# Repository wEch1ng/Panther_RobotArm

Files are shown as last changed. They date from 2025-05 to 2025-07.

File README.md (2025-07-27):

# 一款基于达妙电机和低成本钣金结构件的六轴机械臂

项目初衷是想帮助更多想玩动力学的学生党能玩上低成本的机械臂

有很多同学或RMer实验室有达妙电机，所以方案选择达妙电机，同学们只用出两百五左右的钣金和一些零零碎碎的材料钱就可以了。

基本功能演示视频：https://www.bilibili.com/video/BV1w6dBYxEPu?vd_source=9fd17ff99dc79491d23776f35bfbd4e1

这个仓库仅用于开源最原始的panther机械臂，仅有ros-noetic中一些基本功能：重力补偿模式，拖动示教，基于action通信的moveit轨迹规划
（功能包中的catesian_plan.cpp是调用moveit在笛卡尔空间下画圆，可能有点问题需要自己尝试）

## 相关说明
Panther名字由来：原始设计整机为黑色所以命名为黑豹（Panther），而Panthera是豹类，代表整个Panther机械臂开源项目，希望大家能加入Panthera项目中，创造相对更低成本、性能更好的关节电机方案机械臂，同时实现更多好玩的功能。

## Panthera
后续我们会将Panther从ros中迁移至纯Python环境下来控制

Mujoco仿真及数字孪生

Pinocchio库的使用

diffusion policy模仿学习

强化学习相关内容

跟宇树go2做协同控制

......

后续一些内容的更新在 **Ragtime-LAB** 的Ragtime_Panthera仓库中：
https://github.com/Ragtime-LAB/Ragtime_Panthera

**Ragtime-LAB**目前成员：**亲爱的小一咯**、**小小晨**

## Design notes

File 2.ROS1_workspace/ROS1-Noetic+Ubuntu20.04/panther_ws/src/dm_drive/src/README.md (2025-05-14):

# U2C接入

先插入1-3关节的U2C弹出设备后连接至虚拟机 再插入4-7关节的U2C

ls /dev/ttyACM*
sudo chmod -R 777 /dev/ttyACM*

使用第一条指令

查看是不是弹出

/dev/ttyACM0  /dev/ttyACM1

弹出后再输入第二条指令获得设备使用权限

# 编译工作空间

cd panther_ws/
catkin_make

# 重力补偿

开两个终端分别输入

roscore

rosrun dm_drive ZeroGraMode

# 拖动示教

开两个终端分别输入

roscore

rosrun dm_drive teach

# Moveit控制

开两个终端分别输入

rosrun dm_drive dm_controller

roslaunch panther_moveit_config demo.launch

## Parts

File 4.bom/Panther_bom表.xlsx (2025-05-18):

序号 | 商品名称 | 数量（件） | 单价 | 总计 | 链接
1 | 若干M3螺丝 | 无 | 无 | 无 | https://detail.tmall.com/item.htm?id=601686286684
2 | 若干M3螺母 | 无 | 无 | 无 | 无
 | 橡胶垫片 M3*6*0.8 (200粒) 白 | 1 | 3.4 | 3.4 | https://detail.tmall.com/item.htm?id=20848580632
3 | 达妙4340电机 | 3 | 799 | 2397 | https://item.taobao.com/item.htm?id=775159686012
4 | 达妙4310新手套装 含USB转CAN 转接板 双端线 | 2 | 669 | 1338 | https://item.taobao.com/item.htm?id=730437945135
5 | 达妙4310电机 | 1 | 599 | 599
6 | 达妙3510电机 | 1 | 199 | 199 | https://item.taobao.com/item.htm?abbucket=4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
7 | XT30（2+2）-F母头升级版 | 14 | 1.85 | 25.9 | https://item.taobao.com/item.htm?id=737472229828
8 | 黑色18AWG | 1 | 14 | 14 | https://item.taobao.com/item.htm?id=654286714565
9 | 红色18AWG | 1 | 14 | 14
10 | 黑色28AWG | 1 | 7 | 7
11 | 红色28AWG | 1 | 7 | 7
12 | 滑块 MGW7C（标准块） | 2 | 18 | 36 | https://item.taobao.com/item.htm?id=848276155434&sku_properties=122276018%3A20213
13 | MGW7导轨100MM（备注做成一根200mm的） | 2 | 10 | 20
14 | 1模凸台20齿 内孔10 | 1 | 4.2 | 4.2 | https://detail.tmall.com/item.htm?id=725141098339
15 | 光学平板300x300x13 | 1 | 275 | 275 | https://item.taobao.com/item.htm?from=cart&id=730306309245&skuId=5230836882690&u_channel=null&umpChannel=null
16 | 嘉立创钣金定制 | 5 | 50 | 250 | 立创下单平台
 | 总价 | 5189.5
 | 3D打印材料
 | 兰博abs+
 | https://detail.tmall.com/item.htm?_u=o2rtso892077&id=645580609321&spm=a1z09.2.0.0.40262e8drWVAiV

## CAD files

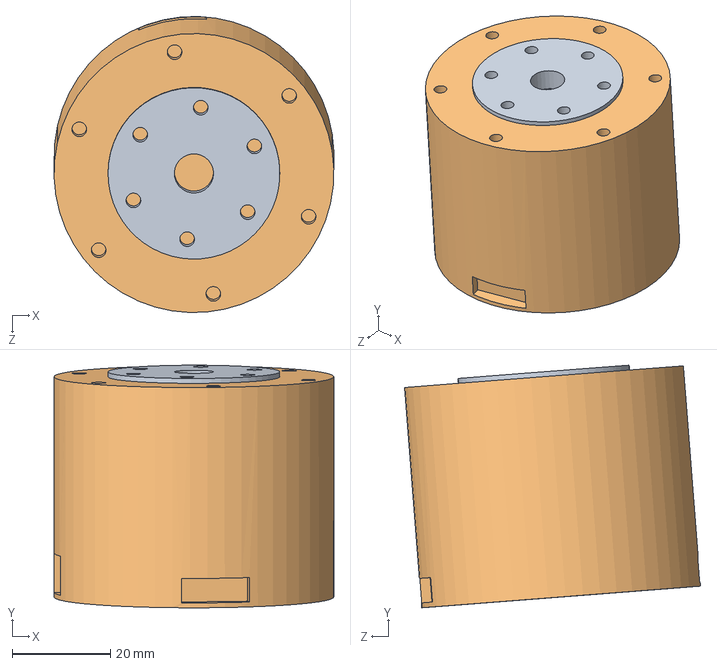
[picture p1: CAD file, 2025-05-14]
1.Model/sw2022/arm/4310电机/4310电机装配体.SLDASM
57.0 x 49.4 x 60.3 mm
4310电机转子
4310电机定子

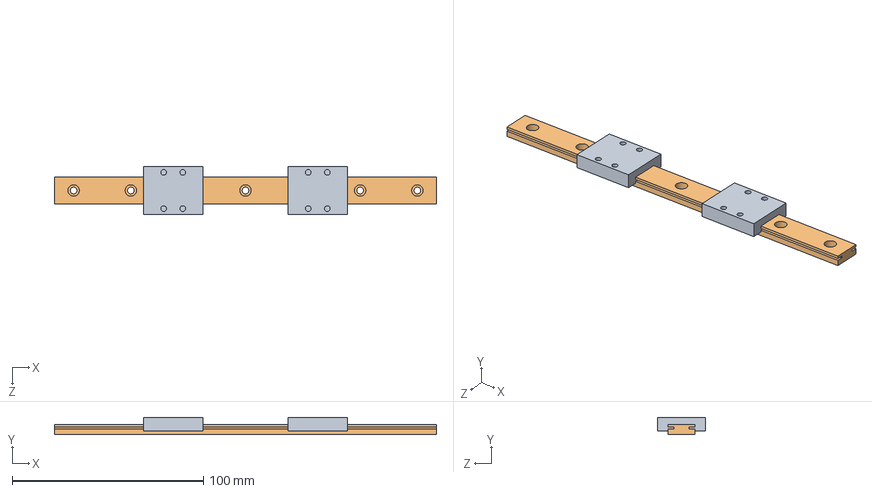
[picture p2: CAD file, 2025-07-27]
1.Model/sw2022/gripper/MGW7导轨滑块模组/MGW7滑轨模组.SLDASM
200.0 x 9.00 x 25.0 mm
MGW7C滑块 x 2
MGW7导轨

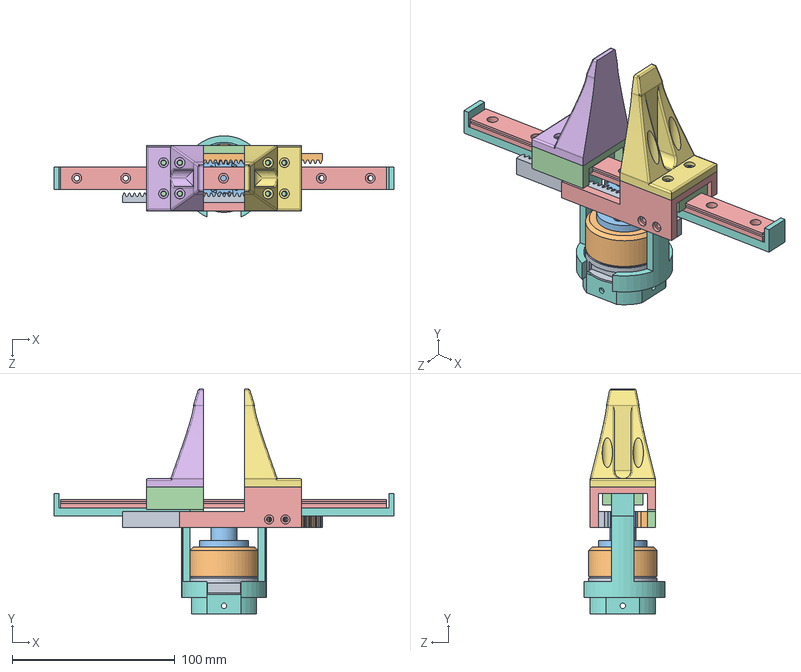
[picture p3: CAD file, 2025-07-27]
1.Model/sw2022/gripper/MyGripper.SLDASM
208.6 x 138.0 x 49.8 mm
3510定子
3510转子
转子齿轮连接件
滑块手指连接件
滑块手指连接件2
手指
镜向手指
夹爪外壳
齿条
齿条2
spur gear_gb
MGW7C滑块 x 2
MGW7导轨

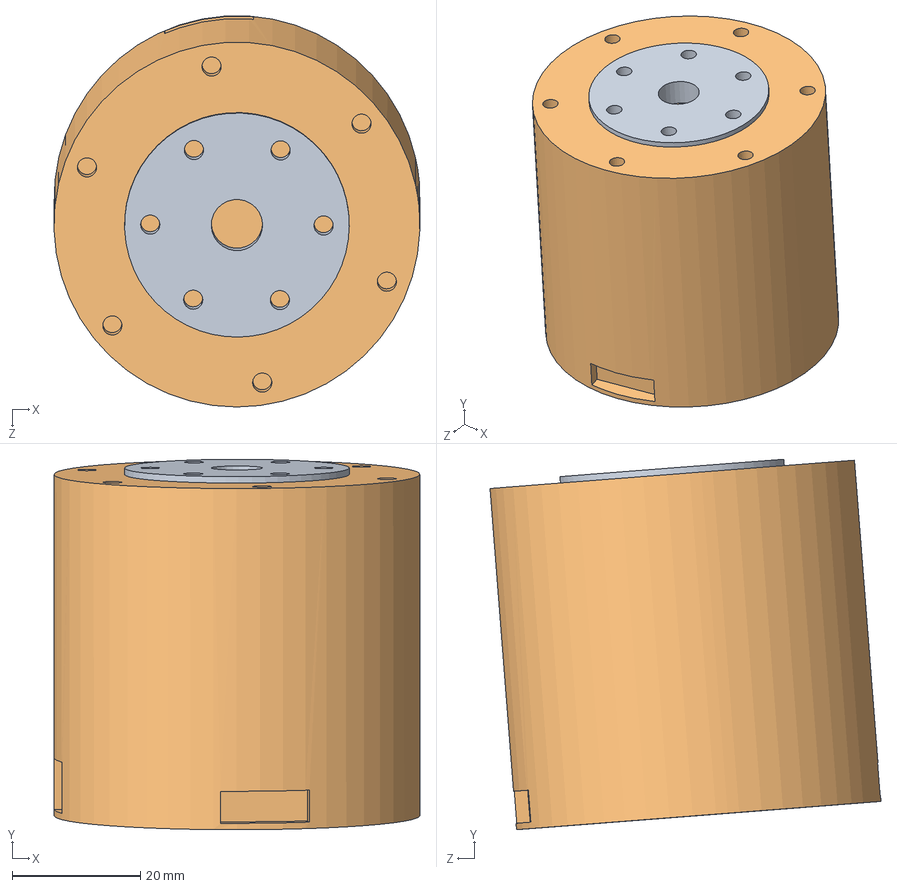
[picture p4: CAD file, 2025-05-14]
1.Model/sw2022/arm/4340电机/4340电机装配体.SLDASM
57.0 x 57.7 x 60.9 mm
4340电机转子
4340电机定子

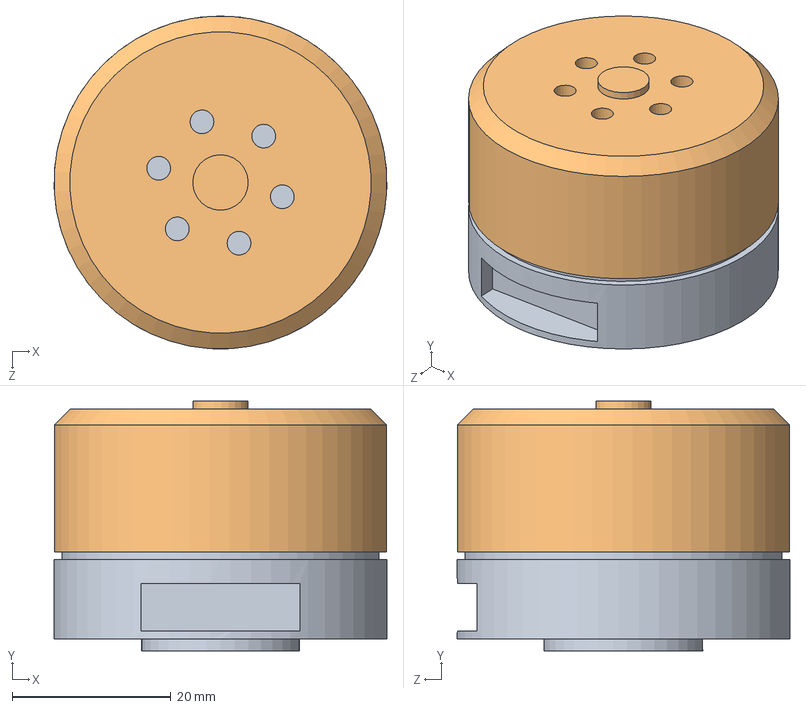
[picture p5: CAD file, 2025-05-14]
1.Model/sw2022/gripper/达妙3510轮毂电机/3510.SLDASM
42.0 x 31.5 x 42.0 mm
3510定子
3510转子

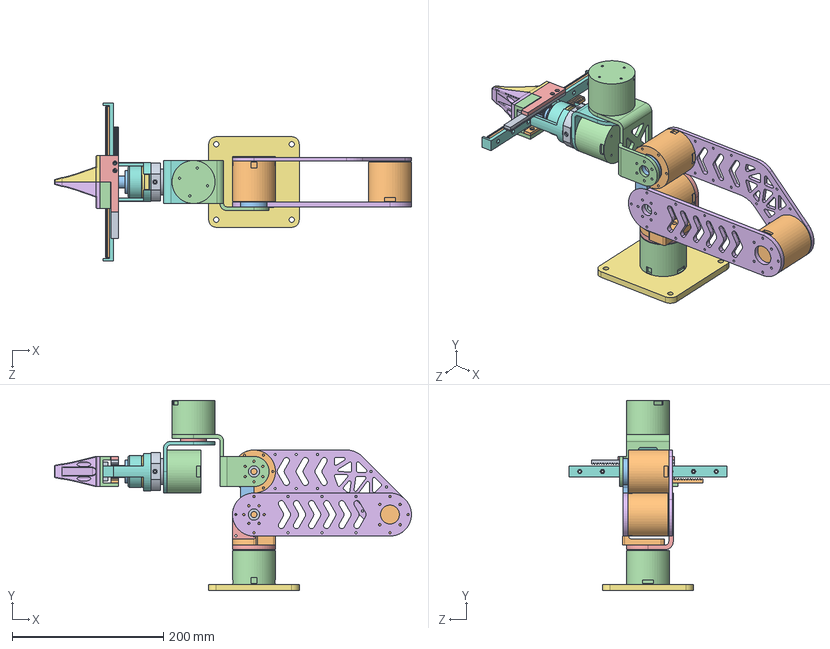
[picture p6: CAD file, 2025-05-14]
1.Model/sw2022/arm/myrobot.SLDASM
472.5 x 251.5 x 208.6 mm
4340电机转子 x 3
4340电机定子 x 3
4310电机转子 x 3
4310电机定子 x 3
一二轴连接件
二三轴连杆
底板
五六轴连接件1
末端法兰
二三轴连杆定位件
四五轴连杆定位件
四五轴连接件_1
五六轴垫块
三四轴连杆
3510定子
3510转子
MGW9C滑块 x 2
MGW9导轨
转子齿轮连接件
滑块手指连接件
滑块手指连接件2
手指
镜向手指
夹爪外壳
齿条
齿条2
spur gear_gb

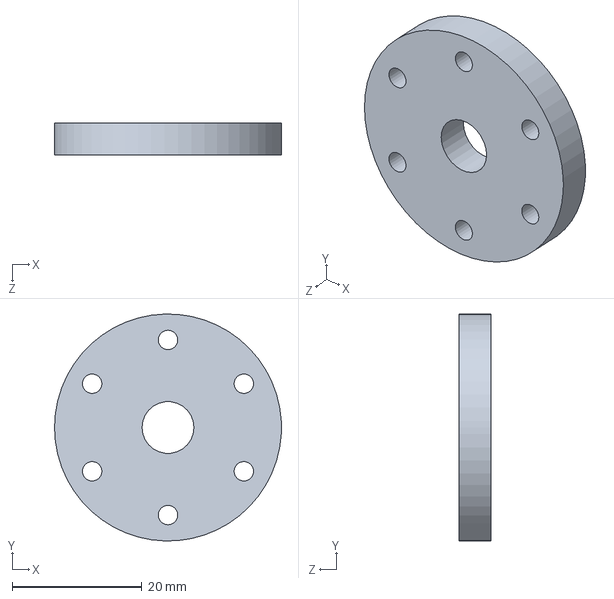
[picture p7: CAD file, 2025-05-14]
1.Model/sw2022/arm/4340电机/4340电机转子.SLDPRT
35.0 x 35.0 x 5.00 mm

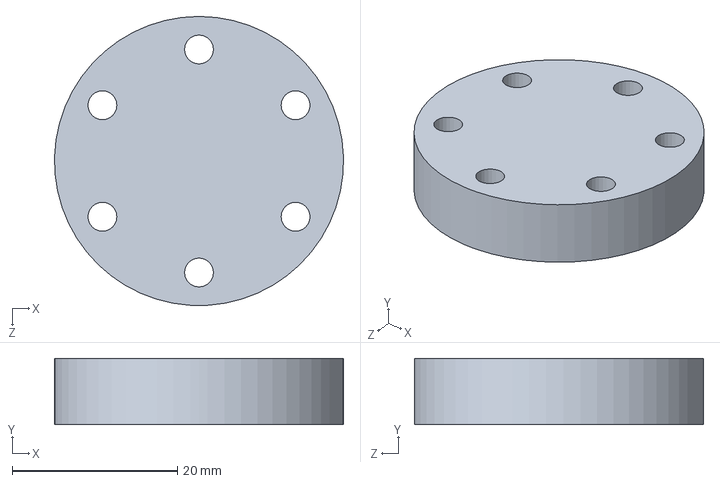
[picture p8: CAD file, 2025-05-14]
1.Model/sw2022/arm/五六轴垫块.SLDPRT
35.0 x 8.00 x 35.0 mm

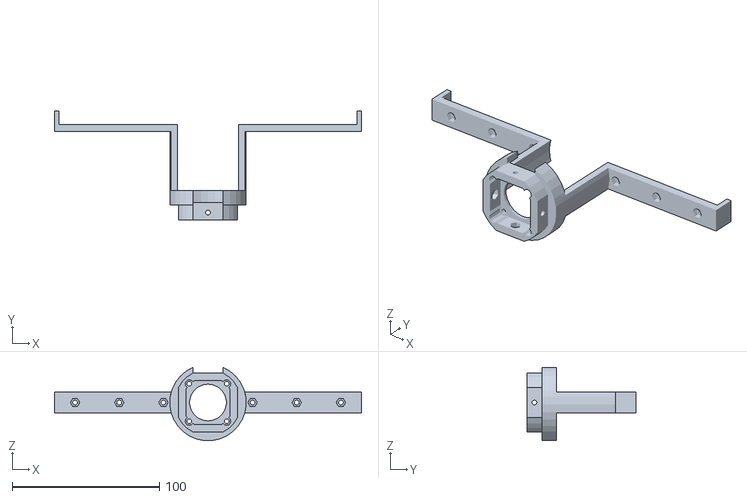
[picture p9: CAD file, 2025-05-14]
1.Model/sw2022/gripper/平行夹爪stl/夹爪外壳.STL
208.6 x 74.0 x 49.7

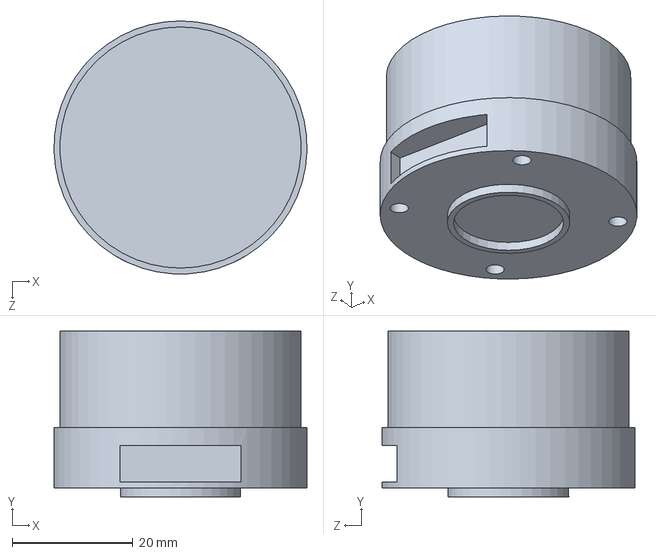
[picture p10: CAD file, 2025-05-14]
1.Model/sw2022/gripper/达妙3510轮毂电机/3510定子.SLDPRT
42.0 x 27.5 x 42.0 mm

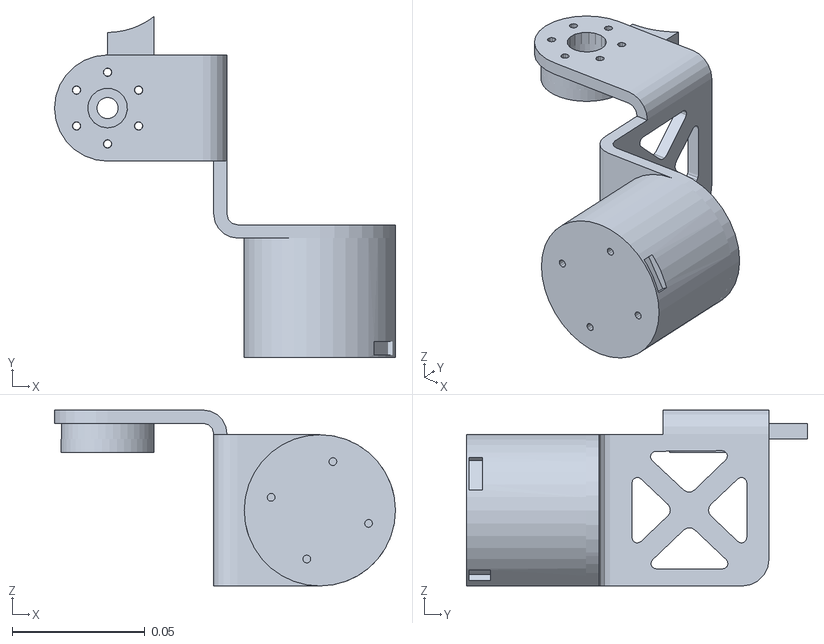
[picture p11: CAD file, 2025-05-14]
2.ROS1_workspace/ROS1-Noetic+Ubuntu20.04/panther_ws/src/panther_description/meshes/link4.STL
0.129 x 0.129 x 0.0663

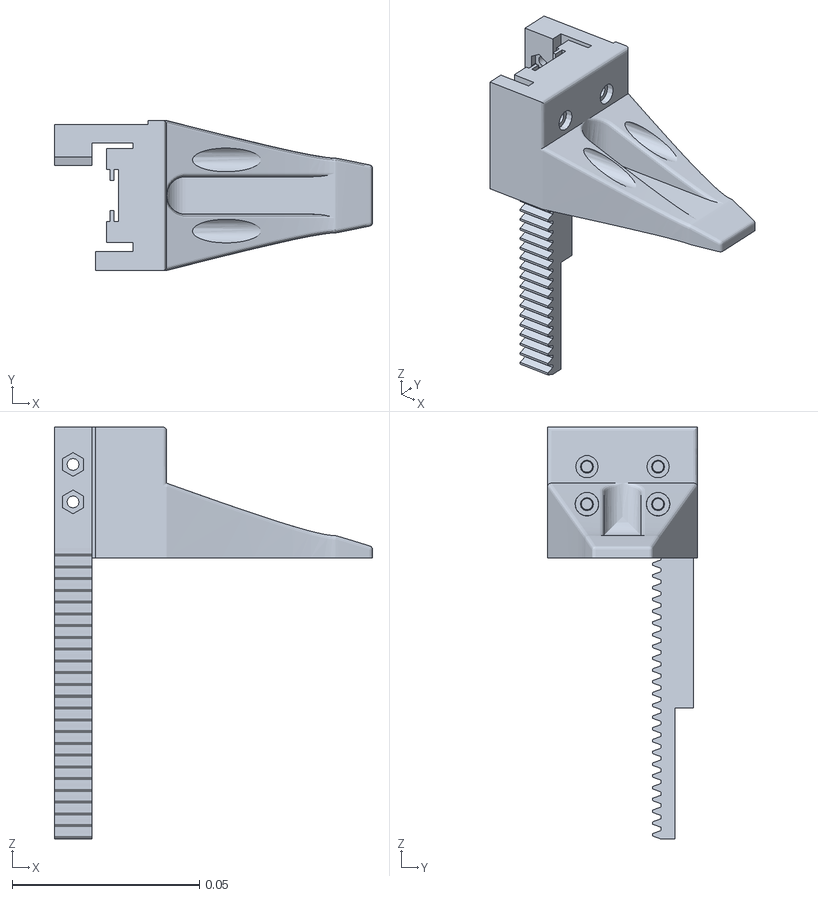
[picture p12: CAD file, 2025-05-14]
3.sw2urdf/panther_description/meshes/gripper_1_link.STL
0.085 x 0.04 x 0.11

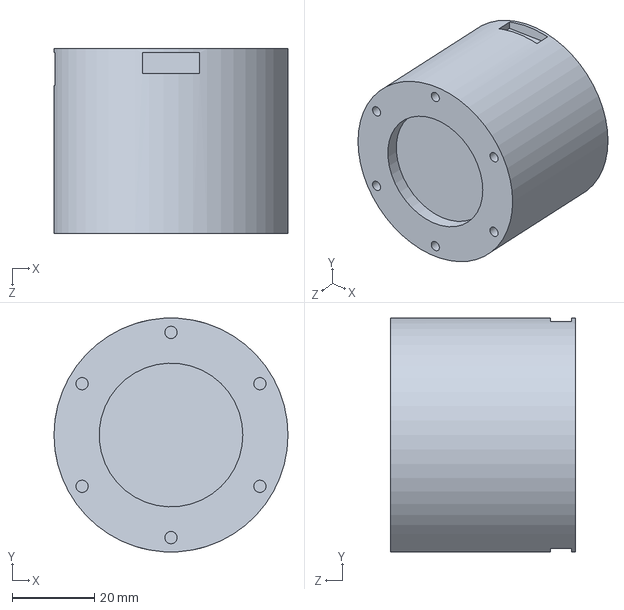
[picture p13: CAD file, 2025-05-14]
1.Model/sw2022/arm/4310电机/4310电机定子.SLDPRT
57.0 x 56.9 x 45.0 mm

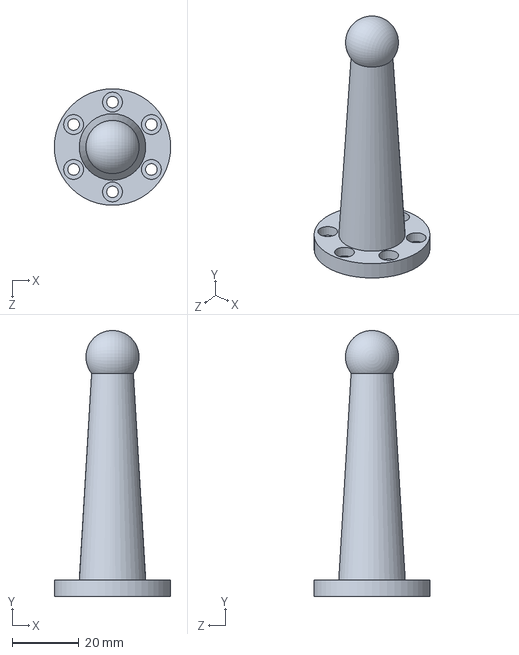
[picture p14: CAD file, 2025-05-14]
1.Model/sw2022/arm/圆头末端.SLDPRT
35.0 x 80.0 x 35.0 mm

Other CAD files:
1.Model/sw2022/arm/装配体1.SLDASM
1.Model/Step/PantherGripper.STEP
1.Model/sw2022/gripper/MGW7导轨滑块模组/MGW7C滑块.SLDPRT
1.Model/sw2022/gripper/平行夹爪stl/齿条.STL
1.Model/sw2022/arm/4310电机/4310电机转子.SLDPRT
1.Model/sw2022/arm/4340电机/4340电机定子.SLDPRT
1.Model/sw2022/arm/一二轴连接件.SLDPRT
1.Model/sw2022/arm/三四轴连杆.SLDPRT
1.Model/sw2022/arm/二三轴连杆.SLDPRT
1.Model/sw2022/arm/二三轴连杆定位件.SLDPRT
1.Model/sw2022/arm/五六轴连接件1.SLDPRT
1.Model/sw2022/arm/从动轴.SLDPRT
1.Model/sw2022/arm/四五轴连接件.SLDPRT
1.Model/sw2022/arm/四五轴连接件_1.SLDPRT
1.Model/sw2022/arm/四五轴连杆定位件.SLDPRT
1.Model/sw2022/arm/底板.SLDPRT
1.Model/sw2022/gripper/1模20齿凸台齿轮.SLDPRT
1.Model/sw2022/gripper/GB - Spur gear 1M 20T 20PA 10FW ---S20A75H50L1.0N.SLDPRT
1.Model/sw2022/gripper/GB - Spur gear 1M 20T 20PA 10FW ---S20B16H18L10.0N.SLDPRT
1.Model/sw2022/gripper/MGW7导轨滑块模组/MGW7导轨.SLDPRT
1.Model/sw2022/gripper/rack spur rectangular_gb.SLDPRT
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

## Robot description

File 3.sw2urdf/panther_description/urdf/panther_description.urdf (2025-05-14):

<?xml version="1.0" encoding="utf-8"?>
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
<robot name="panther_description">
  <link name="base_link">
    <inertial>
      <origin xyz="-5.22421768267327E-17 -4.9646319201852E-06 0.00682594884114425" rpy="0 0 0" />
      <mass value="1.00980967249859" />
      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
    </inertial>
    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
  </link>
  <link name="link1">
    <inertial>
      <origin xyz="-0.000140138460727448 -0.0115178455380478 -0.0189175974816606" rpy="0 0 0" />
      <mass value="0.433540348958132" />
      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
    </inertial>
    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
  </link>
  <joint name="joint1" type="revolute">
    <origin xyz="0 0 0.1005" rpy="0 0 0" />
    <parent link="base_link" />
    <child link="link1" />
    <axis xyz="0 0 1" />
    <limit lower="-3.14" upper="3.14" effort="3" velocity="1" />
  </joint>
  <link name="link2">
    <inertial>
      <origin xyz="0.106425438295557 -3.80251385934116E-12 0.0236077558477278" rpy="0 0 0" />
      <mass value="0.618785138060723" />
      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
    </inertial>
    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
  </link>
  <joint name="joint2" type="revolute">
    <origin xyz="0 0 0" rpy="1.5707963267949 0 3.14159265358979" />
    <parent link="link1" />
    <child link="link2" />
    <axis xyz="0 0 1" />
    <limit lower="-3.14" upper="3.14" effort="3" velocity="1" />
  </joint>
  <link name="link3">
    <inertial>
      <origin xyz="0.112947841031452 0.0109257169593898 0.0234930652223882" rpy="0 0 0" />
      <mass value="0.578438290721478" />
      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
    </inertial>
    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
  </link>
  <joint name="joint3" type="revolute">
    <origin xyz="0.179999999999998 0 0" rpy="3.14159265358979 0 2.83491633418811" />
    <parent link="link2" />
    <child link="link3" />
    <axis xyz="0 0 1" />
    <limit lower="-3.14" upper="3.14" effort="3" velocity="1" />
  </joint>
  <link name="link4">
    <inertial>
      <origin xyz="0.0513406245602283 -0.0329058384127011 0.00868209734629183" rpy="0 0 0" />
      <mass value="0.399529174718196" />
      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
    </inertial>
    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
  </link>
  <joint name="joint4" type="revolute">
    <origin xyz="0.188809427730714 0 0" rpy="3.14159265358979 0 -0.306676319401685" />
    <parent link="link3" />
    <child link="link4" />
    <axis xyz="0 0 1" />
    <limit lower="-3.14" upper="3.14" effort="3" velocity="1" />
  </joint>
  <link name="link5">
    <inertial>
      <origin xyz="2.62314297356869E-16 -0.0160776069634142 -0.0180581657290753" rpy="0 0 0" />
      <mass value="0.321861622200536" />
      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
    </inertial>
    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
  </link>
  <joint name="joint5" type="revolute">
    <origin xyz="0.08 0 0" rpy="-1.5708 1.5708 0" />
    <parent link="link4" />
    <child link="link5" />
    <axis xyz="0 0 1" />
    <limit lower="-3.14" upper="3.14" effort="3" velocity="1" />
  </joint>
  <link name="link6">
    <inertial>
      <origin xyz="-4.35824622879912E-15 -2.3037127760972E-15 -0.0025000000000041" rpy="0 0 0" />
      <mass value="0.00434717883440458" />
      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
    </inertial>
    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
  </link>
  <joint name="joint6" type="revolute">
    <origin xyz="0 -0.036 0" rpy="1.5708 0 0" />
    <parent link="link5" />
    <child link="link6" />
    <axis xyz="0 0 1" />
    <limit lower="-3.14" upper="3.14" effort="3" velocity="1" />
  </joint>
  <link name="gripper_centor_link">
    <inertial>
      <origin xyz="-0.107107907434468 -0.000284330630565321 -3.59780083918573E-09" rpy="0 0 0" />
      <mass value="0.105344961426715" />
      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
    </inertial>
    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
  </link>
  <joint name="gripper_centor_joint" type="fixed">
    <origin xyz="0 0 0.148" rpy="0 -1.5708 0" />
    <parent link="link6" />
    <child link="gripper_centor_link" />
    <axis xyz="0 0 0" />
    <limit lower="-3.14" upper="3.14" effort="3" velocity="1" />
  </joint>
  <link name="gripper_1_link">
    <inertial>
      <origin xyz="-0.0574118738630709 0.00266477929541095 0.00735600840817693" rpy="0 0 0" />
      <mass value="0.0426889603072748" />
      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
    </inertial>
    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
  </link>
  <joint name="gripper_1_joint" type="prismatic">
    <origin xyz="0 0 0.148" rpy="0 -1.5708 0" />
    <parent link="link6" />
    <child link="gripper_1_link" />
    <axis xyz="0 0 1" />
    <limit lower="0" upper="0.06" effort="0.18" velocity="1" />
  </joint>
  <link name="gripper_2_link">
    <inertial>
      <origin xyz="-0.0573873207529981 -0.00294326456557495 -0.00756965143896882" rpy="0 0 0" />
      <mass value="0.0427537416759649" />
      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
    </inertial>
    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
  </link>
  <joint name="gripper_2_joint" type="prismatic">
    <origin xyz="0 0 0.148" rpy="0 -1.5708 0" />
    <parent link="link6" />
    <child link="gripper_2_link" />
    <axis xyz="0 0 1" />
    <limit lower="0" upper="0.06" effort="0.18" velocity="1" />
    <mimic joint="gripper_1_joint" multiplier="-1" offset="0" />
  </joint>
</robot>

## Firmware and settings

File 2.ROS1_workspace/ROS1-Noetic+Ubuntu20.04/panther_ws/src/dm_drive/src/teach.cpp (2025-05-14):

#include "ros/ros.h"
#include "6Dof_dyna.h"
#include "damiao.h"
#include "unistd.h"
#include <cmath>
#include <algorithm> // for std::max and std::min
#include <iostream>  // for std::cout
#include <thread>
#include <boost/thread/shared_mutex.hpp>
#include "sensor_msgs/JointState.h"
#include <vector>
#include <fstream>
#include <atomic>
#include <array>


// 硬件控制参数
constexpr double RECORD_RATE = 500.0;    // 记录频率
constexpr double RECORD_DURATION = 20.0; // 记录时长
constexpr double RETURN_SPEED = 0.5;     // 返回速度比例

// 单个关节状态数据结构
struct JointState {
    double position;    // 关节位置（弧度）
    double velocity;    // 关节速度（弧度/秒）
};

// 单帧数据（所有关节+时间戳）
struct JointFrame {
    double timestamp;   // 时间戳（相对于记录开始时间）
    std::array<JointState, 7> joints; // 6个关节状态
};

// 全局数据存储
std::vector<JointFrame> motion_buffer; // 动作数据缓冲区
std::array<double, 7> initial_positions; // 初始关节位置（弧度）

// 硬件控制对象
damiao::Motor M1(damiao::DM4310,0x01, 0x11);
damiao::Motor M2(damiao::DM4340,0x02, 0x12);
damiao::Motor M3(damiao::DM4340,0x03, 0x13);
damiao::Motor M4(damiao::DM4340,0x04, 0x14);
damiao::Motor M5(damiao::DM4310,0x05, 0x15);
damiao::Motor M6(damiao::DM4310,0x06, 0x16);
damiao::Motor M7(damiao::DMH3510,0x07, 0x17);

damiao::Motor motors[] = {M1, M2, M3, M4, M5, M6, M7};

// boost::shared_mutex serial_mutex_;  
std::shared_ptr<SerialPort> serial1;
std::shared_ptr<SerialPort> serial2;
damiao::Motor_Control dm1(serial1);
damiao::Motor_Control dm2(serial2);

void add_all_motors(){
    dm1.addMotor(&M1);
    dm1.addMotor(&M2);
    dm1.addMotor(&M3);
    dm2.addMotor(&M4);
    dm2.addMotor(&M5);
    dm2.addMotor(&M6);
    dm2.addMotor(&M7);
}

void change_motor_mode_MIT(){
    dm1.switchControlMode(M1,damiao::MIT_MODE);
    dm1.switchControlMode(M2,damiao::MIT_MODE);
    dm1.switchControlMode(M3,damiao::MIT_MODE);
    dm2.switchControlMode(M4,damiao::MIT_MODE);
    dm2.switchControlMode(M5,damiao::MIT_MODE);
    dm2.switchControlMode(M6,damiao::MIT_MODE);
}

void change_motor_mode_PosVel(){
    dm1.switchControlMode(M1,damiao::POS_VEL_MODE);
    dm1.switchControlMode(M2,damiao::POS_VEL_MODE);
    dm1.switchControlMode(M3,damiao::POS_VEL_MODE);
    dm2.switchControlMode(M4,damiao::POS_VEL_MODE);
    dm2.switchControlMode(M5,damiao::POS_VEL_MODE);
    dm2.switchControlMode(M6,damiao::POS_VEL_MODE);
}

void enable_all_motors() {
    // dm1.enable(M1);
    // dm1.enable(M2);
    // dm1.enable(M3);
    // dm2.enable(M4);
    // dm2.enable(M5);
    dm2.enable(M6);
    // dm2.enable(M7);
    ROS_INFO("All motors enabled");
}

void disable_all_motors() {
    dm1.disable(M1);
    dm1.disable(M2);
    dm1.disable(M3);
    dm2.disable(M4);
    dm2.disable(M5);
    dm2.disable(M6);
    dm2.disable(M7);
}

void refresh_motor_states() {
    dm1.refresh_motor_status(M1);
    dm1.refresh_motor_status(M2);
    dm1.refresh_motor_status(M3);
    dm2.refresh_motor_status(M4);
    dm2.refresh_motor_status(M5);
    dm2.refresh_motor_status(M6);
    dm2.refresh_motor_status(M7);
}

// 根据关节索引获取位置（示例实现）
double get_joint_position(int index) {
    switch(index) {
        case 0: return M1.Get_Position();
        case 1: return M2.Get_Position();
        case 2: return M3.Get_Position();
        case 3: return M4.Get_Position();
        case 4: return M5.Get_Position();
        case 5: return M6.Get_Position();
        case 6: return M7.Get_Position();
        default: throw std::out_of_range("Invalid joint index");
    }
}

// 根据关节索引获取速度（示例实现） 
double get_joint_velocity(int index) {
    switch(index) {
        case 0: return M1.Get_Velocity();
        case 1: return M2.Get_Velocity();
        case 2: return M3.Get_Velocity();
        case 3: return M4.Get_Velocity();
        case 4: return M5.Get_Velocity();
        case 5: return M6.Get_Velocity();
        case 6: return M7.Get_Velocity();
        default: throw std::out_of_range("Invalid joint index");
    }
}

void record_phase() {
    ROS_INFO("Start recording for %.1f seconds...", RECORD_DURATION);
    
    // 切换到MIT模式（力矩控制模式，便于被动拖动）
    change_motor_mode_MIT();

    ros::Rate rate(RECORD_RATE);
    ros::Time start_time = ros::Time::now();
    ros::Time last_print_time = start_time;
    
    while((ros::Time::now() - start_time).toSec() < RECORD_DURATION) {
        double q[7] = {0,0,0,0,0,0,0};
        double vel[7] = {0,0,0,0,0,0,0};
        double f[6] = {0,0,0,0,0,0};
        // 刷新电机状态（从硬件读取最新数据）
        refresh_motor_states();
        
        // 构建当前帧数据
        JointFrame frame;
        frame.timestamp = (ros::Time::now() - start_time).toSec();
        
        // 填充6个关节数据
        for(int i=0; i<7; ++i) {
            // 注意：这里需要根据实际电机对象调整获取方式
            frame.joints[i] = {
                .position = get_joint_position(i),  // 需要实现获取函数
                .velocity = get_joint_velocity(i)   // 需要实现获取函数
            };
            q[i] = get_joint_position(i);
            vel[i] = get_joint_velocity(i);
        }
        if(vel[0]<-0.006)  f[0] = 0.06*vel[0];
        if(vel[0]>0.006)   f[0] = 0.06*vel[0];

        if(vel[1]<-0.006)  f[1] = -0.1+0.05*vel[1];
        if(vel[1]>0.006)   f[1] = 0.1+0.05*vel[1];

        if(vel[2]<-0.006)  f[2] = -0.2+0.1*vel[2];
        if(vel[2]>0.006)   f[2] = 0.2+0.1*vel[2];

        if(vel[3]<-0.006)  f[3] = -0.30+0.2*vel[3];
        if(vel[3]>0.006)   f[3] = 0.30+0.2*vel[3];

        if(vel[4]<-0.01)  f[4] = 0.03-0.05*vel[4];
        if(vel[4]>0.01)   f[4] = -0.03-0.05*vel[4];

        // Calculate gravity compensation
        VectorXd tau = compute_gravity_compensation(q);
        tau[0] = tau[0] + f[0];
        tau[1] = tau[1] + f[1];
        tau[2] = tau[2] + f[2];
        tau[3] = tau[3] + f[3];
        tau[4] = tau[4] + f[4];
        tau[5] = tau[5] + f[5];
        //臂
        dm1.control_mit(M1, 0.0, 0.0, 0.0, 0.0, tau[0]);
        dm1.control_mit(M2, 0.0, 0.0, 0.0, 0.0, tau[1]);
        dm1.control_mit(M3, 0.0, 0.0, 0.0, 0.0, tau[2]);
        dm2.control_mit(M4, 0.0, 0.0, 0.0, 0.0, tau[3]);
        dm2.control_mit(M5, 0.0, 0.0, 0.0, 0.0, tau[4]);
        dm2.control_mit(M6, 0.0, 0.0, 0.0, 0.0, tau[5]);
        //夹爪
        dm2.control_pos_force(M7,0,0,0);

        // 每秒打印进度
        if ((ros::Time::now() - last_print_time).toSec() >= 1.0) {
            ROS_INFO("Recording progress: %.1f/%.1f seconds", 
                    frame.timestamp, RECORD_DURATION);
            last_print_time = ros::Time::now();
        }

        // 添加实时关节角度显示
        // ROS_INFO_THROTTLE(0.5,  // 每0.5秒显示一次
        //     "Joints[rad]: %.3f, %.3f, %.3f, %.3f, %.3f, %.3f",
        //     frame.joints[0].position,
        //     frame.joints[1].position,
        //     frame.joints[2].position,
        //     frame.joints[3].position,
        //     frame.joints[4].position,
        //     frame.joints[5].position
        //     frame.joints[6].position
        // );
        ROS_INFO_THROTTLE(0.5,  // 每0.5秒显示一次
            "vel[rad]: %.3f, %.3f, %.3f, %.3f, %.3f, %.3f",
            frame.joints[0].velocity,
            frame.joints[1].velocity,
            frame.joints[2].velocity,
            frame.joints[3].velocity,
            frame.joints[4].velocity,
            frame.joints[5].velocity,
            frame.joints[6].velocity
        );

        // 存入缓冲区
        motion_buffer.push_back(frame);
        
        // 保持400Hz记录频率
        rate.sleep();
    }
    
    ROS_INFO("Recording completed. Saved %lu frames", motion_buffer.size());
}

void save_recording(const std::string& filename) {
    std::ofstream file(filename);
    file << "timestamp,j1_pos,j1_vel,...,j6_pos,j6_vel\n";
    for (const auto& frame : motion_buffer) {
        file << frame.timestamp;
        for (const auto& joint : frame.joints) {
            file << "," << joint.position << "," << joint.velocity;
        }
        file << "\n";
    }
    ROS_INFO("Data saved to %s", filename.c_str());
}

/**
 * @brief 控制机械臂返回初始位置
 * @param slow_return 返回模式标志位
 *                    true: 慢速渐变返回（防止急动）
 *                    false: 快速直接定位返回
 */
void return_to_initial(bool slow_return) {
    ROS_INFO("Returning to initial positions...");
    
    // 切换到位置-速度控制模式（确保平稳移动）
    change_motor_mode_PosVel();

    // 控制循环参数配置
    ros::Rate rate(200);        // 控制频率200Hz（5ms周期）
    constexpr int STEPS = 800;  // 总控制步数（慢速模式时总时间=200步*5ms=1秒）

    // 分步控制循环
    for(int step=0; step<STEPS; ++step) {
        // 遍历所有6个关节
        for(int i=0; i<7; ++i) {
            // 计算位置插值比例因子
            // slow_return模式：从0到1的线性渐变（step=0时ratio=0.005, step=199时ratio=1.0）
            // 快速模式：直接使用ratio=1.0（一步到位）
            double ratio = slow_return ? 
                static_cast<double>(step+1)/STEPS : // 慢速渐变
                1.0;                                // 直接定位

            // 计算目标位置（线性插值公式）:
            // target = 初始位置 * 比例 + 当前位置 * (1 - 比例)
            // 当ratio从0→1时，目标位置从当前位置→初始位置
            double target = initial_positions[i] * ratio + 
                           motors[i].Get_Position() * (1.0 - ratio);

            // 根据关节所属控制器发送控制指令
            if(i < 3) {
                // 前3个关节使用dm1控制器
                // control_pos_vel参数：电机对象，目标位置，速度比例（0.0-1.0）
                dm1.control_pos_vel(motors[i], target, 0.3);
            } 
            else if((i >= 3) && (i < 6)) {
                // 后3个关节使用dm2控制器
                dm2.control_pos_vel(motors[i], target, 0.3);
            }
            else if (i == 6) {
                dm2.control_pos_force(motors[i],2.0,500,500);
            }
        }
        // 维持控制频率
        rate.sleep();
    }

    // dm1.control_pos_vel(motors[0], 0.0, 0.0);
    // dm1.control_pos_vel(motors[1], 0.0, 0.0);
    // dm1.control_pos_vel(motors[2], 0.0, 0.0);
    // dm2.control_pos_vel(motors[3], 0.0, 0.0);
    // dm2.control_pos_vel(motors[4], 0.0, 0.0);
    // dm2.control_pos_vel(motors[5], 0.0, 0.0);
    sleep(2);// 等待2秒
}

void replay_phase() {
    ROS_INFO("Starting motion replay...");
    
    // 切换到位置-速度模式
    // change_motor_mode_PosVel();
    // 切换到MIT模式
    change_motor_mode_MIT();

    ros::Rate rate(RECORD_RATE);
    size_t frame_counter = 0;
    
    while(frame_counter < motion_buffer.size() && ros::ok()) {
        auto& frame = motion_buffer[frame_counter];
        double current_pos[7];

        // 刷新电机状态（从硬件读取最新数据）
        refresh_motor_states();
        for(int i=0; i<7; ++i) {
                current_pos[i] = get_joint_position(i);  // 需要实现获取函数
        }

        // 添加复现位置显示
        ROS_INFO_THROTTLE(0.5, 
            "Replaying[rad]: %.5lf, %.5lf, %.5lf, %.5lf, %.5lf, %.5lf",
            current_pos[0],
            current_pos[1],
            current_pos[2],
            current_pos[3],
            current_pos[4],
            current_pos[5],
            current_pos[6]
        );

        VectorXd tau = compute_gravity_compensation(current_pos);

        // 设置每个关节的位置和速度
        for(int i=0; i<7; ++i) {
            const auto& state = frame.joints[i];
            // if(i < 3) {
            //     dm1.control_pos_vel(
            //         motors[i], 
            //         state.position,
            //         state.velocity
            //     );
            // } else {
            //     dm2.control_pos_vel(
            //         motors[i],
            //         state.position,
            //         state.velocity
            //     );
            // }
            
            if(i==0){
                dm1.control_mit(motors[i], 25.0, 1.5, state.position, state.velocity, tau[0]);
            }
            if(i==1){
                dm1.control_mit(motors[i], 52.0, 1.0, state.position, state.velocity, tau[1]);//110
            }
            if(i==2){
                dm1.control_mit(motors[i], 65.0, 1.5, state.position, state.velocity, tau[2]);//140
            }
            if(i==3){
                dm2.control_mit(motors[i], 40.0, 1.0, state.position, state.velocity, tau[3]);//120
            }
            if(i==4){
                dm2.control_mit(motors[i], 10.0, 1.0, state.position, state.velocity, tau[4]);
            }
            if(i==5){
                dm2.control_mit(motors[i], 10.0, 1.0, state.position, state.velocity, tau[5]);
            }
            if(i==6){
                //夹紧距离减小0.2保证能夹住东西
                dm2.control_pos_force(motors[i],state.position-0.2,abs(state.velocity*100),500);
            }
            
            // if(i==0) dm1.control_pos_vel(
            //     motors[i], 
            //     state.position,
            //     state.velocity
            // );
            // if(i==1) dm1.control_pos_vel(
            //     motors[i], 
            //     state.position,
            //     state.velocity
            // );
            // if(i==2) dm1.control_pos_vel(
            //     motors[i], 
            //     state.position,
            //     state.velocity
            // );
            // if(i==3) dm2.control_pos_vel(
            //     motors[i], 
            //     state.position,
            //     state.velocity
            // );
            // if(i==4) dm2.control_pos_vel(
            //     motors[i], 
            //     state.position,
            //     state.velocity
            // );
            // if(i==5) dm2.control_pos_vel(
            //     motors[i], 
            //     state.position,
            //     state.velocity
            // );
        }
        ++frame_counter;
        rate.sleep();
    }
    
    ROS_INFO("Replay completed");
}

int main(int argc, char** argv) {
    ros::init(argc, argv, "teach");
    ros::NodeHandle nh;  // 添加ROS节点句柄初始化

    serial1 = std::make_shared<SerialPort>("/dev/ttyACM0", B921600);
    serial2 = std::make_shared<SerialPort>("/dev/ttyACM1", B921600);
    dm1 = damiao::Motor_Control(serial1);
    dm2 = damiao::Motor_Control(serial2);
    
    add_all_motors();
    enable_all_motors();
    
    // 获取初始位置
    // refresh_motor_states();
    // for(int i=0; i<6; ++i) {
    //     initial_positions[i] = motors[i].Get_Position();
    // }
    initial_positions ={0,0,0,0,0,0,2.0};


    // 主执行流程
    return_to_initial(true); // 阶段：慢速回初始
    record_phase();        // 阶段1：记录动作
    return_to_initial(true); // 阶段2：慢速回初始
    replay_phase();        // 阶段3：复现动作
    return_to_initial(true);// 阶段4：快速回初始
    save_recording("motion_data.csv");
    
    disable_all_motors();
    return 0;
}

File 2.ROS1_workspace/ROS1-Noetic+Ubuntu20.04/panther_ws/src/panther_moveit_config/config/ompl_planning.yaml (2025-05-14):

planner_configs:
  AnytimePathShortening:
    type: geometric::AnytimePathShortening
    shortcut: true  # Attempt to shortcut all new solution paths
    hybridize: true  # Compute hybrid solution trajectories
    max_hybrid_paths: 24  # Number of hybrid paths generated per iteration
    num_planners: 4  # The number of default planners to use for planning
    planners: ""  # A comma-separated list of planner types (e.g., "PRM,EST,RRTConnect"Optionally, planner parameters can be passed to change the default:"PRM[max_nearest_neighbors=5],EST[goal_bias=.5],RRT[range=10. goal_bias=.1]"
  SBL:
    type: geometric::SBL
    range: 0.0  # Max motion added to tree. ==> maxDistance_ default: 0.0, if 0.0, set on setup()
  EST:
    type: geometric::EST
    range: 0.0  # Max motion added to tree. ==> maxDistance_ default: 0.0, if 0.0 setup()
    goal_bias: 0.05  # When close to goal select goal, with this probability. default: 0.05
  LBKPIECE:
    type: geometric::LBKPIECE
    range: 0.0  # Max motion added to tree. ==> maxDistance_ default: 0.0, if 0.0, set on setup()
    border_fraction: 0.9  # Fraction of time focused on boarder default: 0.9
    min_valid_path_fraction: 0.5  # Accept partially valid moves above fraction. default: 0.5
  BKPIECE:
    type: geometric::BKPIECE
    range: 0.0  # Max motion added to tree. ==> maxDistance_ default: 0.0, if 0.0, set on setup()
    border_fraction: 0.9  # Fraction of time focused on boarder default: 0.9
    failed_expansion_score_factor: 0.5  # When extending motion fails, scale score by factor. default: 0.5
    min_valid_path_fraction: 0.5  # Accept partially valid moves above fraction. default: 0.5
  KPIECE:
    type: geometric::KPIECE
    range: 0.0  # Max motion added to tree. ==> maxDistance_ default: 0.0, if 0.0, set on setup()
    goal_bias: 0.05  # When close to goal select goal, with this probability. default: 0.05
    border_fraction: 0.9  # Fraction of time focused on boarder default: 0.9 (0.0,1.]
    failed_expansion_score_factor: 0.5  # When extending motion fails, scale score by factor. default: 0.5
    min_valid_path_fraction: 0.5  # Accept partially valid moves above fraction. default: 0.5
  RRT:
    type: geometric::RRT
    range: 0.0  # Max motion added to tree. ==> maxDistance_ default: 0.0, if 0.0, set on setup()
    goal_bias: 0.05  # When close to goal select goal, with this probability? default: 0.05
  RRTConnect:
    type: geometric::RRTConnect
    range: 0.0  # Max motion added to tree. ==> maxDistance_ default: 0.0, if 0.0, set on setup()
  RRTstar:
    type: geometric::RRTstar
    range: 0.0  # Max motion added to tree. ==> maxDistance_ default: 0.0, if 0.0, set on setup()
    goal_bias: 0.05  # When close to goal select goal, with this probability? default: 0.05
    delay_collision_checking: 1  # Stop collision checking as soon as C-free parent found. default 1
  TRRT:
    type: geometric::TRRT
    range: 0.0  # Max motion added to tree. ==> maxDistance_ default: 0.0, if 0.0, set on setup()
    goal_bias: 0.05  # When close to goal select goal, with this probability? default: 0.05
    max_states_failed: 10  # when to start increasing temp. default: 10
    temp_change_factor: 2.0  # how much to increase or decrease temp. default: 2.0
    min_temperature: 10e-10  # lower limit of temp change. default: 10e-10
    init_temperature: 10e-6  # initial temperature. default: 10e-6
    frontier_threshold: 0.0  # dist new state to nearest neighbor to disqualify as frontier. default: 0.0 set in setup()
    frontier_node_ratio: 0.1  # 1/10, or 1 nonfrontier for every 10 frontier. default: 0.1
    k_constant: 0.0  # value used to normalize expresssion. default: 0.0 set in setup()
  PRM:
    type: geometric::PRM
    max_nearest_neighbors: 10  # use k nearest neighbors. default: 10
  PRMstar:
    type: geometric::PRMstar
  FMT:
    type: geometric::FMT
    num_samples: 1000  # number of states that the planner should sample. default: 1000
    radius_multiplier: 1.1  # multiplier used for the nearest neighbors search radius. default: 1.1
    nearest_k: 1  # use Knearest strategy. default: 1
    cache_cc: 1  # use collision checking cache. default: 1
    heuristics: 0  # activate cost to go heuristics. default: 0
    extended_fmt: 1  # activate the extended FMT*: adding new samples if planner does not finish successfully. default: 1
  BFMT:
    type: geometric::BFMT
    num_samples: 1000  # number of states that the planner should sample. default: 1000
    radius_multiplier: 1.0  # multiplier used for the nearest neighbors search radius. default: 1.0
    nearest_k: 1  # use the Knearest strategy. default: 1
    balanced: 0  # exploration strategy: balanced true expands one tree every iteration. False will select the tree with lowest maximum cost to go. default: 1
    optimality: 1  # termination strategy: optimality true finishes when the best possible path is found. Otherwise, the algorithm will finish when the first feasible path is found. default: 1
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

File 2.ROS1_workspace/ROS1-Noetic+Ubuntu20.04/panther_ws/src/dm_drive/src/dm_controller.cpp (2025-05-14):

#include <ros/ros.h>
#include <actionlib/server/simple_action_server.h>
#include <control_msgs/FollowJointTrajectoryAction.h>
#include <sensor_msgs/JointState.h>
#include <shared_mutex>
#include <mutex>
#include <boost/thread/shared_mutex.hpp>
#include <queue>
#include <thread>  
#include <std_msgs/Float32MultiArray.h>
#include <iostream>
#include <moveit_msgs/RobotTrajectory.h>
#include <vector>
#include <trajectory_msgs/JointTrajectory.h>
#include <ros/duration.h>
#include "std_msgs/String.h"
#include "damiao.h"
#include "unistd.h"
#include <cmath>
#include <algorithm> // for std::max and std::min
#include <iostream>  // for std::cout
#include <array>
#include <iostream>
#include <eigen3/Eigen/Dense>
#include <cmath>
#include "6Dof_dyna.h"
#include <Eigen/Core>
#include <algorithm>

using namespace Eigen;
using namespace std;

// 控制参数
const double POSITION_TOLERANCE = 0.06;   // 弧度
const double TIME_TOLERANCE = 0.1;        // 秒
const double MAX_DELAY_COMPENSATION = 0.5;// 最大延时补偿

// 自定义三次样条插值类
class CubicSpline {
    private:
        std::vector<double> x_, y_;  // 原始数据点
        std::vector<double> b_, c_, d_;  // 样条系数
    
    public:
        // 设置数据点
        void set_points(const std::vector<double>& x, const std::vector<double>& y) {
            if (x.size() != y.size()) {
                throw std::invalid_argument("x and y must have the same size");
            }
            if (x.size() < 2) {
                throw std::invalid_argument("At least 2 points are required");
            }
    
            x_ = x;
            y_ = y;
            int n = x.size();
            b_.resize(n);
            c_.resize(n);
            d_.resize(n);
    
            // 计算系数
            std::vector<double> h(n - 1), alpha(n - 1);
            for (int i = 0; i < n - 1; ++i) {
                h[i] = x[i + 1] - x[i];
                alpha[i] = (y[i + 1] - y[i]) / h[i];
            }
    
            std::vector<double> l(n), mu(n), z(n);
            l[0] = 1;
            for (int i = 1; i < n - 1; ++i) {
                l[i] = 2 * (x[i + 1] - x[i - 1]) - h[i - 1] * mu[i - 1];
                mu[i] = h[i] / l[i];
                z[i] = (alpha[i] - alpha[i - 1] - h[i - 1] * z[i - 1]) / l[i];
            }
    
            l[n - 1] = 1;
            z[n - 1] = 0;
            c_[n - 1] = 0;
    
            for (int j = n - 2; j >= 0; --j) {
                c_[j] = z[j] - mu[j] * c_[j + 1];
                b_[j] = (y[j + 1] - y[j]) / h[j] - h[j] * (c_[j + 1] + 2 * c_[j]) / 3;
                d_[j] = (c_[j + 1] - c_[j]) / (3 * h[j]);
            }
        }
    
        // 插值计算
        double operator()(double x) const {
            auto it = std::upper_bound(x_.begin(), x_.end(), x);
            int idx = std::max(int(it - x_.begin()) - 1, 0);
            double dx = x - x_[idx];
            return y_[idx] + b_[idx] * dx + c_[idx] * dx * dx + d_[idx] * dx * dx * dx;
        }

        double derivative(double x) const {
            auto it = std::upper_bound(x_.begin(), x_.end(), x);
            int idx = std::max(int(it - x_.begin()) - 1, 0);
            double dx = x - x_[idx];
            return b_[idx] + 2 * c_[idx] * dx + 3 * d_[idx] * dx * dx;
        }
    };

class HybridTrigger {
    private:
        bool use_time_based_ = true;    // 初始基于时间触发
        double position_tolerance_ = 0.05;
        double max_time_error_ = 0.1;    // 最大时间误差
        
    public:
        bool shouldSendNextPoint(const ros::Time& expected_time,
                                const std::vector<double>& current_pos,
                                const std::vector<double>& target_pos) 
        {
            // 时间误差超过阈值时切换为位置触发
            double time_error = fabs((ros::Time::now() - expected_time).toSec());
            if(time_error > max_time_error_){
                use_time_based_ = false;
            }
    
            // 位置接近目标时切换回时间触发
            bool position_ok = checkPosition(current_pos, target_pos);
            if(position_ok && !use_time_based_){
                use_time_based_ = true;
            }
    
            return use_time_based_ ? (ros::Time::now() >= expected_time) : position_ok;
        }
        bool checkPosition(const std::vector<double>& target, const std::vector<double>& actual) const {
            if (target.size() != actual.size()) {
                ROS_ERROR("Target and actual positions have different sizes!");
            return false;
            }

            for (size_t i = 0; i < target.size(); ++i) {
                if (fabs(target[i] - actual[i]) > POSITION_TOLERANCE) {
                    return false;
                }
            }
            return true;
        }
};

class DmController {
private:
    // 硬件接口
    // 新增串口操作锁
    boost::shared_mutex serial_mutex_;  
    damiao::Motor M1, M2, M3, M4, M5, M6,M7;
    std::shared_ptr<SerialPort> serial1;
    std::shared_ptr<SerialPort> serial2;
    damiao::Motor_Control dm1;
    damiao::Motor_Control dm2;
    std::vector<CubicSpline> splines_;

    // ROS 接口
    ros::Publisher joint_state_pub_;
    actionlib::SimpleActionServer<control_msgs::FollowJointTrajectoryAction> as_;
    actionlib::SimpleActionServer<control_msgs::FollowJointTrajectoryAction> gripper_as_;
    
    // 共享数据
    boost::shared_mutex data_mutex_;
    std::queue<trajectory_msgs::JointTrajectoryPoint> trajectory_queue_;
    sensor_msgs::JointState current_joint_state_;
    bool trajectory_running_ = false;
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

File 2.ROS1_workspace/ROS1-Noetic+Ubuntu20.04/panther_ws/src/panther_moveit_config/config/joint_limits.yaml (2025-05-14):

# joint_limits.yaml allows the dynamics properties specified in the URDF to be overwritten or augmented as needed

# For beginners, we downscale velocity and acceleration limits.
# You can always specify higher scaling factors (<= 1.0) in your motion requests.  # Increase the values below to 1.0 to always move at maximum speed.
default_velocity_scaling_factor: 0.1
default_acceleration_scaling_factor: 0.1

# Specific joint properties can be changed with the keys [max_position, min_position, max_velocity, max_acceleration]
# Joint limits can be turned off with [has_velocity_limits, has_acceleration_limits]
joint_limits:
  gripper_1_joint:
    has_velocity_limits: true
    max_velocity: 1
    has_acceleration_limits: false
    max_acceleration: 0
  gripper_2_joint:
    has_velocity_limits: true
    max_velocity: 1
    has_acceleration_limits: false
    max_acceleration: 0
  joint1:
    has_velocity_limits: true
    max_velocity: 1
    has_acceleration_limits: false
    max_acceleration: 0
  joint2:
    has_velocity_limits: true
    max_velocity: 1
    has_acceleration_limits: false
    max_acceleration: 0
  joint3:
    has_velocity_limits: true
    max_velocity: 1
    has_acceleration_limits: false
    max_acceleration: 0
  joint4:
    has_velocity_limits: true
    max_velocity: 1
    has_acceleration_limits: false
    max_acceleration: 0
  joint5:
    has_velocity_limits: true
    max_velocity: 1
    has_acceleration_limits: false
    max_acceleration: 0
  joint6:
    has_velocity_limits: true
    max_velocity: 1
    has_acceleration_limits: false
    max_acceleration: 0

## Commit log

2025-05-14 Panther Update
    Panther Update
    [1模20齿凸台齿轮.SLDPRT, 3510.SLDASM, 3510定子.SLDPRT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]
2025-07-27 修复导轨型号名错误
    [MGW7C滑块.SLDPRT, MGW7导轨.SLDPRT, MGW7滑轨模组.SLDASM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]
